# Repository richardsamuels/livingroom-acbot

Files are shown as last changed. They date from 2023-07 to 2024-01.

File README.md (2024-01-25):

# AC Bot
An ESPHome-based robot to integrate my GE AEL08LQQ2 window AC into Home Assistant.

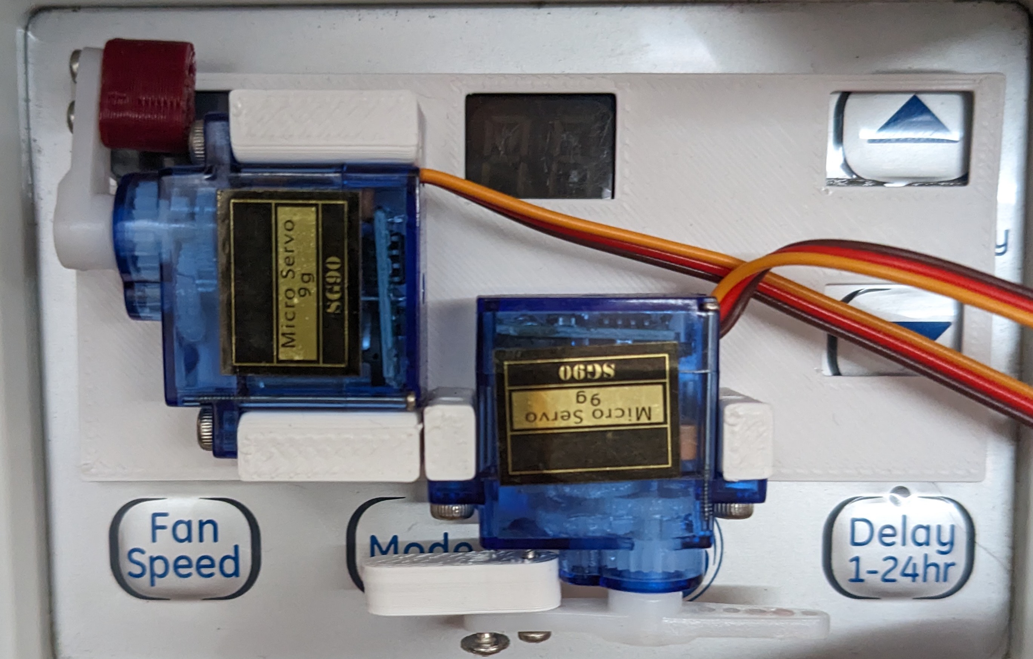
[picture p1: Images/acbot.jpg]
ACbot installed in place


## Custom PCB
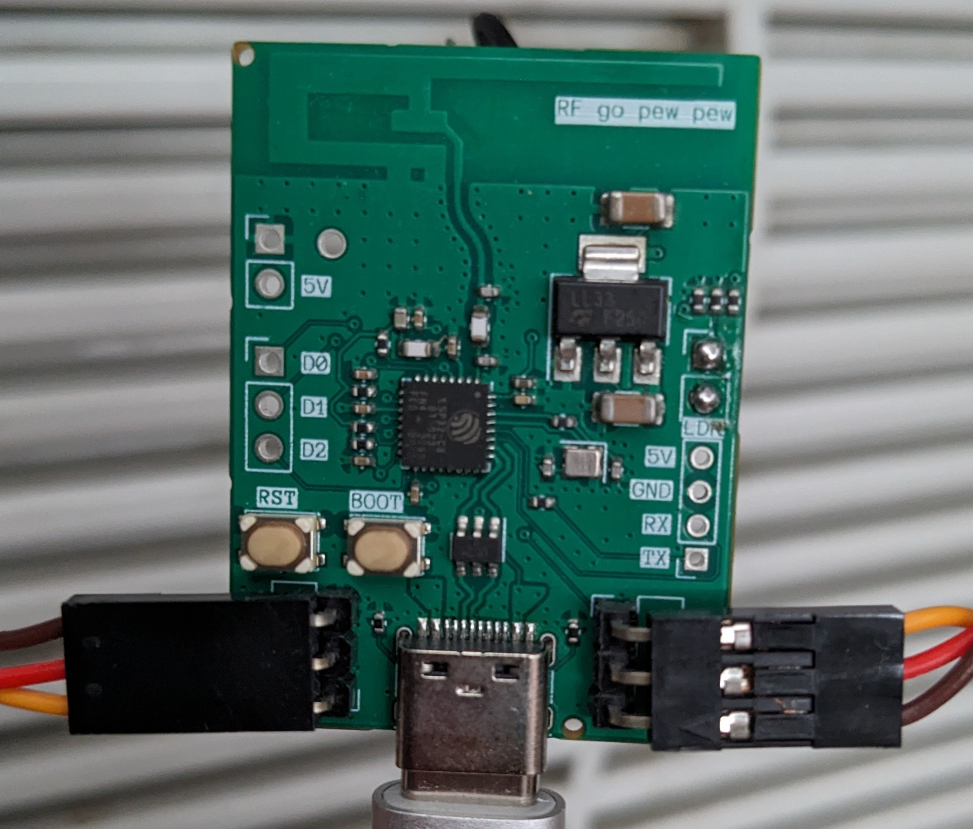
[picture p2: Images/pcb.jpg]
PCB


A custom PCB can be found in ./PCB. The expected servo pinout is (Control, 5V, GND),
where Control is indicated on the silkscreen with a solid colored pin.

## BOM

Note: This BOM does not include parts on custom PCB. See the JLCPCB-compatible
[PCB BOM](PCB/jlcpcb/production_files/BOM-esp.csv) for those items, which can
be used to purchase a fully assembled PCB from JLCPCB.

| Part | Quantity |
| --- | --- |
| SG90 Servo | 2 |
| M2.5x6 SHCS | 4 |
| M2x10 self-tapping screws | 5 |
| [~Photoresistor~*](https://www.amazon.com/gp/product/B01N7V536K) | 1 |
| STL/panel.stl, any stiff filament (ABS, PLA, or PETG) | 1 |
| STL/power-pusher.stl, any stiff filament (ABS, PLA, or PETG) | 2 |

* The original version of this PCB used a photoresistor to detect the on/off
state of the AC, see below for the flaws of this approach

## 3D Printed Parts

1. Connect all servos to the flashed PCB and apply power via USB-C to zero the
servo positions.
2. To each servo, attach power-pusher.stl to the servo horn with a single arm
using M2x10 self-tappers. Use the hole farthest from the center, and third from
the end.
3. Attach servos with M2.5x6 SHCS bolts to panel.stl. Screw directly into the
plastic.
4. Using VHB, or similarly strong double-sided sticky tape, attach directly to
AC's front panel, ensuring alignment with the power, temperature read out, and
temperature control buttons.
5. Press the panel down with even more force to ensure the servos will not push
the printed parts off the front panel.

## Failed Approaches
1. This project originally used a photoresistor to detect when the temperature
readout was lit to infer the on/off state of the air conditioner. This approach
proved unreliable because the outer plastic shell of the airconditioner is
translucent to sunlight, and would provide false indications when the sun
shined directly on the air conditioner's shell.

This was remediated with an [Aqara Smart Plug](https://www.amazon.com/gp/product/B07CJ2MM6Z)
which reports the power consumption in watts.. If the AC is consuming more than
50 watts, it is considered to be on; otherwise, it is considered to be off.

2 . The original version of this project offered the ability to change the
temperature instead of the AC mode (Cool/Energy Save/Fan). After putting v1
into action, I did not use the remote temperature change functionality, but
wanted to change the mode. This functionality was dropped, and the servo was
repurposed to allow changing the mode instead.

## Future Work
1. Change the AC Mode instead of turning off the entire unit when Home
Assistant's thermostat is used.
2. Design a proper mounting mechanism for the PCB, and a cover for the whole
unit

# Setup & Flashing
## Setup
1. `python -m venv venv`
2. `./venv/bin/activate`
3. `python -m pip install esphome`
## Flashing
`esphome run livingroom-acbot.yaml`

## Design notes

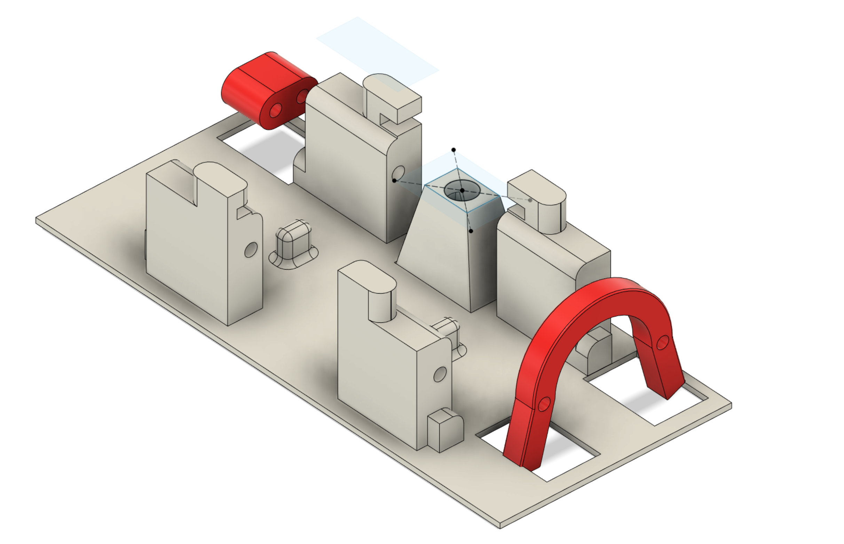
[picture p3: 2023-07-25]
Images/fusion.png

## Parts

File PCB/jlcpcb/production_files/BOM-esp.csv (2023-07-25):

Comment | Designator | Footprint | LCSC
22uF | C301,C302 | C_1206_3216Metric | C12891
10n | C204 | C_0402_1005Metric | C15195
0.1u | C206,C207,C208,C209,C210,C211 | C_0402_1005Metric | C1525
12p | C212,C213 | C_0402_1005Metric | C1547
10u | C205 | C_0402_1005Metric | C15525
3p3 | C201,C202 | C_0402_1005Metric | C1565
USB_C_Plug_USB2.0 | P301 | USB_C_Receptacle_HRO_TYPE-C-31-M-12 | C165948
22R | R207 | R_0402_1005Metric | C25092
470R | R201 | R_0402_1005Metric | C25117
Crystal_GND24 | Y201 | Crystal_SMD_2016-4Pin_2.0x1.6mm | C255898
5k1 | R202,R203,R204,R205,R206,R301,R302,R303,R304 | R_0402_1005Metric | C25905
2n2 | L201,L202 | L_0603_1608Metric | C29682
LDL111733R | U301 | SOT-223-3_TabPin2 | C435835
SW_Push | SW201,SW202 | SW_SPST_PTS810 | C470426
ESP32-C3FN4 | U201 | QFN-32-1EP_5x5mm_P0.5mm_EP3.45x3.45mm | C5143572
1u | C203 | C_0402_1005Metric | C52923
USBLC6-2SC6 | U302 | SOT-23-6 | C7519
Conn_01x03_Pin | J101,J102 | PinHeader_1x03_P2.54mm_Horizontal | C92159
50k | R101 | PinHeader_1x02_P2.54mm_Vertical
2.4GHz aerial | AE201 | Texas_SWRU120D_InvF_2.4GHz_Right
Conn_01x04_Socket | J104 | PinSocket_1x04_P2.00mm_Vertical
Conn_01x03_Socket | J105 | PinHeader_1x03_P2.54mm_Vertical
Conn_01x02_Socket | J103 | PinHeader_1x02_P2.54mm_Vertical

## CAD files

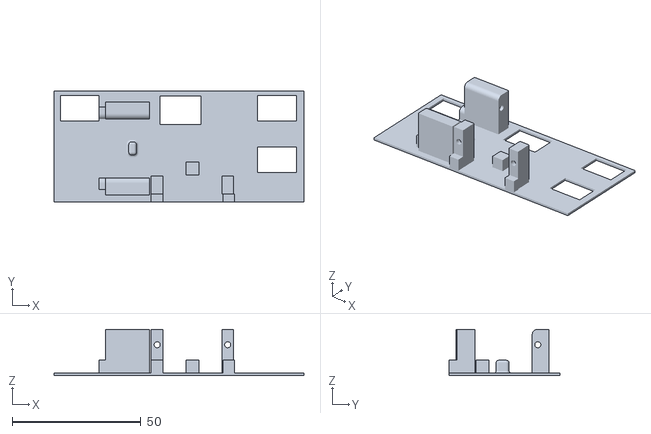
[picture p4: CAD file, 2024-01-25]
STL/panel.stl
97.0 x 43.0 x 18.0

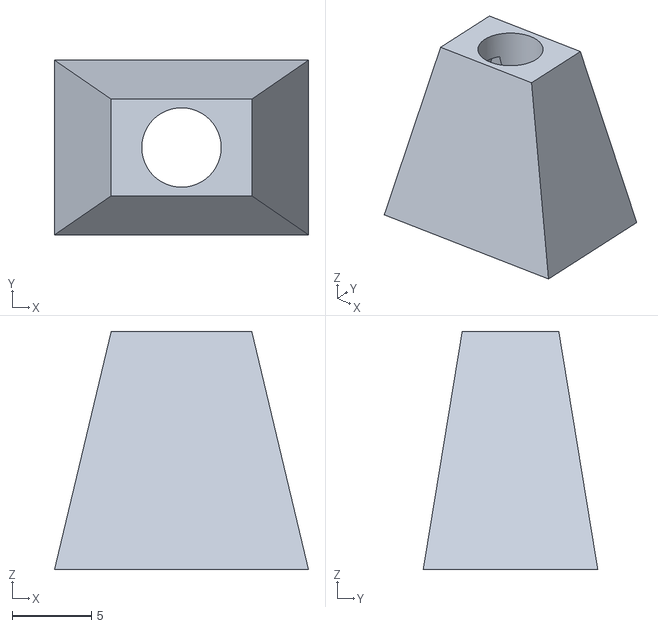
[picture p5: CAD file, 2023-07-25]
STL/photoresistor-guide.stl
16.0 x 11.0 x 15.0

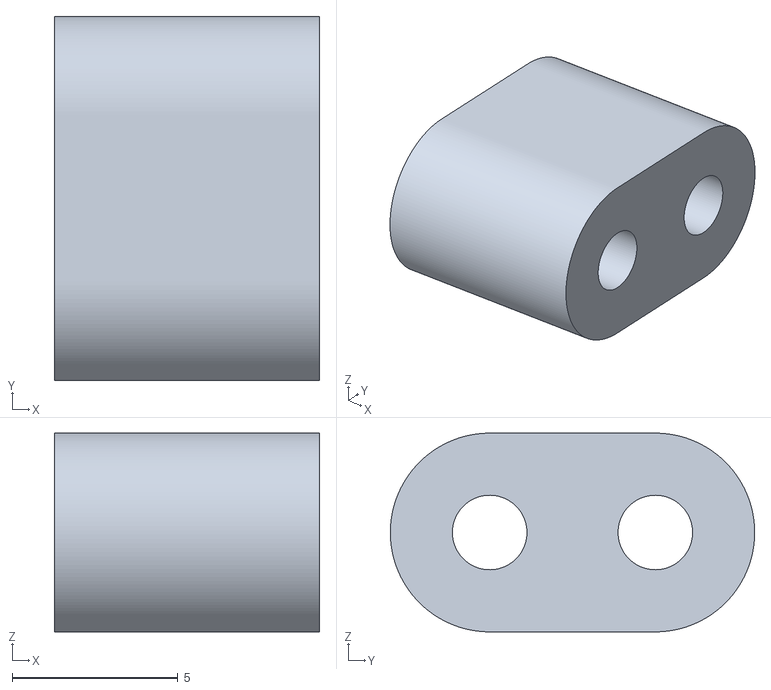
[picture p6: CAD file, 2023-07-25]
STL/power-pusher.stl
8.00 x 11.0 x 6.00

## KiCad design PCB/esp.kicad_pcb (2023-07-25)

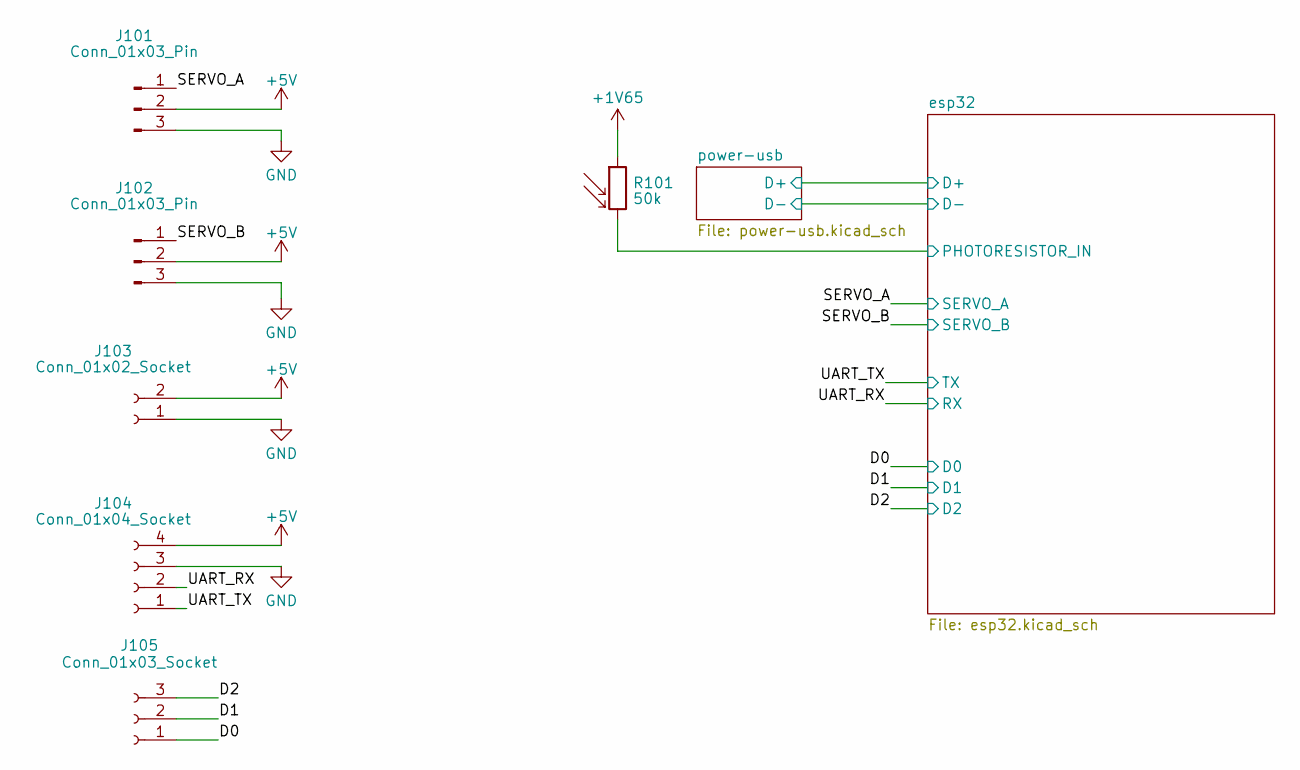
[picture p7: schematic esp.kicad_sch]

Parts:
J101, J102: Conn_01x03_Pin; PinHeader_1x03_P2.54mm_Horizontal
J103: Conn_01x02_Socket; PinHeader_1x02_P2.54mm_Vertical
J104: Conn_01x04_Socket; PinSocket_1x04_P2.00mm_Vertical
J105: Conn_01x03_Socket; PinHeader_1x03_P2.54mm_Vertical
R101: 50k; PinHeader_1x02_P2.54mm_Vertical

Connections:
+1V65: R101.1; also elsewhere on the board
+5V: J101.2, J102.2, J103.2, J104.4; also elsewhere on the board
/D0: J105.1; also elsewhere on the board
/D1: J105.2; also elsewhere on the board
/D2: J105.3; also elsewhere on the board
/SERVO_A: J101.1; also elsewhere on the board
/SERVO_B: J102.1; also elsewhere on the board
/UART_RX: J104.2; also elsewhere on the board
/UART_TX: J104.1; also elsewhere on the board
/esp32/PHOTORESISTOR_IN: R101.2; also elsewhere on the board
GND: J101.3, J102.3, J103.1, J104.3; also elsewhere on the board

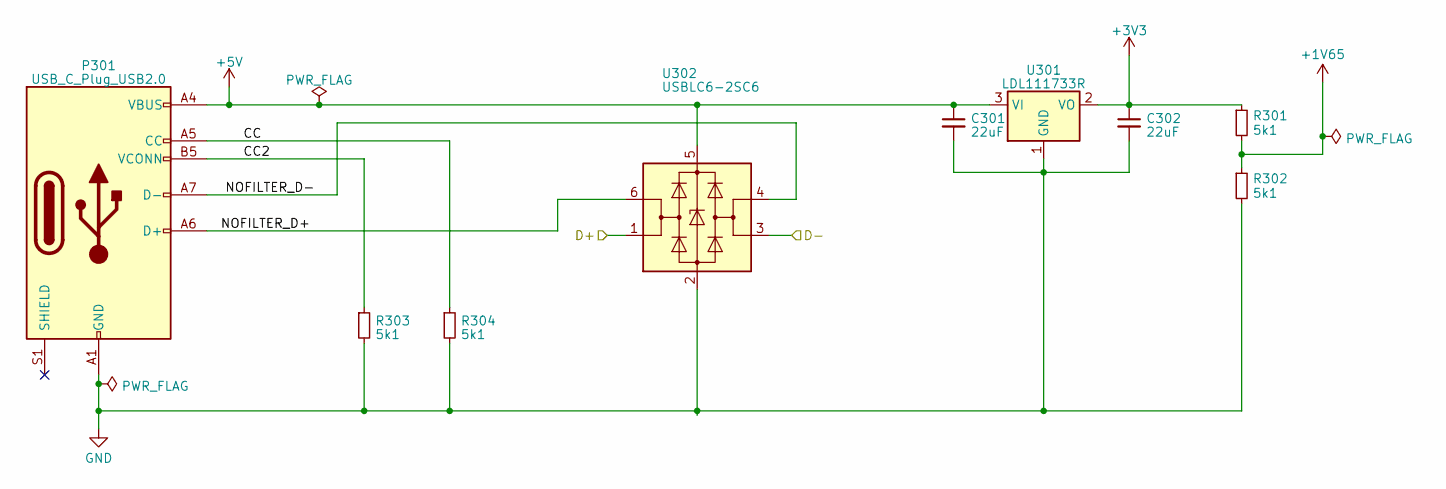
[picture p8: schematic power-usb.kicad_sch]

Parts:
C301, C302: 22uF; C_1206_3216Metric
P301: USB_C_Plug_USB2.0; USB_C_Receptacle_HRO_TYPE-C-31-M-12
R301, R302, R303, R304: 5k1; R_0402_1005Metric
U301: LDL111733R; SOT-223-3_TabPin2
U302: USBLC6-2SC6; SOT-23-6

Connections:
+1V65: R301.2, R302.1; also elsewhere on the board
+3V3: C302.1, R301.1, U301.2 (VO); also elsewhere on the board
+5V: C301.1, P301.A4 (VBUS), P301.A9 (VBUS), P301.B4 (VBUS), P301.B9 (VBUS), U301.3 (VI), U302.5 (VBUS); also elsewhere on the board
/esp32/D+: U302.1 (I/O1); also elsewhere on the board
/esp32/D-: U302.3 (I/O2); also elsewhere on the board
/power-usb/CC: P301.A5 (CC), R304.1
/power-usb/CC2: P301.B5 (VCONN), R303.1
/power-usb/NOFILTER_D+: P301.A6 (D+), P301.B6 (D+), U302.6 (I/O1)
/power-usb/NOFILTER_D-: P301.A7 (D-), P301.B7 (D-), U302.4 (I/O2)
GND: C301.2, C302.2, P301.A1 (GND), P301.A12 (GND), P301.B1 (GND), P301.B12 (GND), R302.2, R303.2, R304.2, U301.1 (GND), U302.2 (GND); also elsewhere on the board

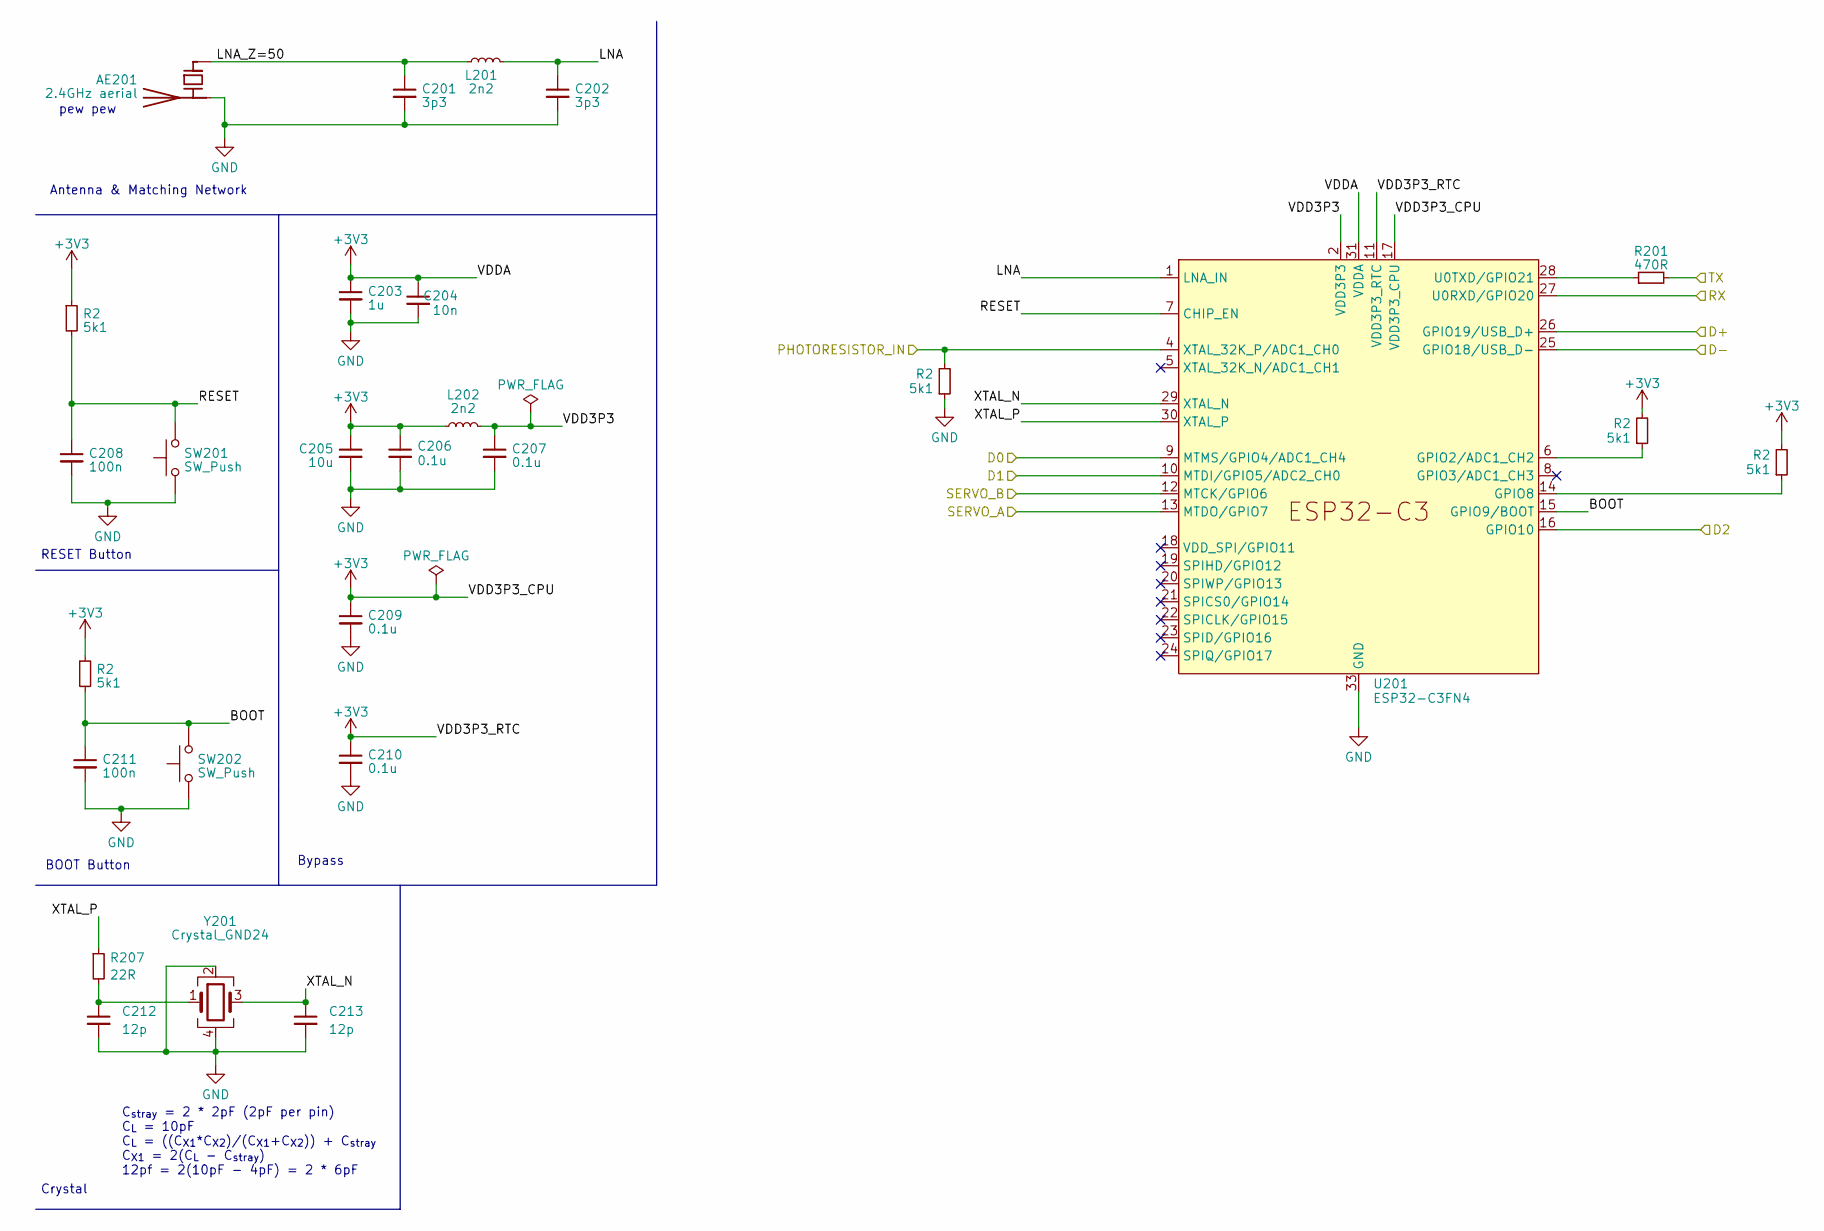
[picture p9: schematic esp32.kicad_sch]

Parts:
AE201: 2.4GHz aerial; Texas_SWRU120D_InvF_2.4GHz_Right
C201, C202: 3p3; C_0402_1005Metric
C203: 1u; C_0402_1005Metric
C204: 10n; C_0402_1005Metric
C205: 10u; C_0402_1005Metric
C206, C207, C209, C210: 0.1u; C_0402_1005Metric
C208, C211: 100n; C_0402_1005Metric
C212, C213: 12p; C_0402_1005Metric
L201, L202: 2n2; L_0603_1608Metric
R2: 5k1; R_0402_1005Metric
R201: 470R; R_0402_1005Metric
R207: 22R; R_0402_1005Metric
SW201, SW202: SW_Push; SW_SPST_PTS810
U201: ESP32-C3FN4; QFN-32-1EP_5x5mm_P0.5mm_EP3.45x3.45mm
Y201: Crystal_GND24; Crystal_SMD_2016-4Pin_2.0x1.6mm

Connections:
+3V3: C203.1, C204.1, C205.1, C206.1, C209.1, C210.1, L202.1, U201.11 (VDD3P3_RTC), U201.17 (VDD3P3_CPU), U201.31 (VDDA), U201.32 (VDDA); also elsewhere on the board
/D0: U201.9 (MTMS/GPIO4/ADC1_CH4); also elsewhere on the board
/D1: U201.10 (MTDI/GPIO5/ADC2_CH0); also elsewhere on the board
/D2: U201.16 (GPIO10); also elsewhere on the board
/SERVO_A: U201.13 (MTDO/GPIO7); also elsewhere on the board
/SERVO_B: U201.12 (MTCK/GPIO6); also elsewhere on the board
/UART_RX: U201.27 (U0RXD/GPIO20); also elsewhere on the board
/UART_TX: R201.2; also elsewhere on the board
/esp32/BOOT: C211.1, SW202.2, U201.15 (GPIO9/BOOT); also elsewhere on the board
/esp32/D+: U201.26 (GPIO19/USB_D+); also elsewhere on the board
/esp32/D-: U201.25 (GPIO18/USB_D-); also elsewhere on the board
/esp32/LNA: C202.1, L201.2, U201.1 (LNA_IN)
/esp32/LNA_Z=50: AE201.1 (FEED), C201.1, L201.1
/esp32/PHOTORESISTOR_IN: U201.4 (XTAL_32K_P/ADC1_CH0); also elsewhere on the board
/esp32/RESET: C208.1, SW201.2, U201.7 (CHIP_EN); also elsewhere on the board
/esp32/VDD3P3: C207.1, L202.2, U201.2 (VDD3P3), U201.3 (VDD3P3)
/esp32/XTAL_N: C213.1, U201.29 (XTAL_N), Y201.3
/esp32/XTAL_P: R207.1, U201.30 (XTAL_P)
GND: AE201.2 (PCB_Trace), C201.2, C202.2, C203.2, C204.2, C205.2, C206.2, C207.2, C208.2, C209.2, C210.2, C211.2, C212.2, C213.2, SW201.1, SW202.1, U201.33 (GND), Y201.2, Y201.4; also elsewhere on the board
unnamed: C212.1, R207.2, Y201.1
unnamed 26: U201.6 (GPIO2/ADC1_CH2); also elsewhere on the board
unnamed 27: U201.14 (GPIO8); also elsewhere on the board
unnamed: R201.1, U201.28 (U0TXD/GPIO21)

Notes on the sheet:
Antenna & Matching Network
C_{stray} = 2 * 2pF (2pF per pin) C_{L} = 10pF C_{L} = ((C_{X1}*C_{X2})/(C_{X1}+C_{X2})) + C_{stray} C_{X1} = 2(C_{L} - C_{stray}) 12pf = 2(10pF - 4pF) = 2 * 6pF
Crystal
RESET Button
Bypass
BOOT Button
pew pew

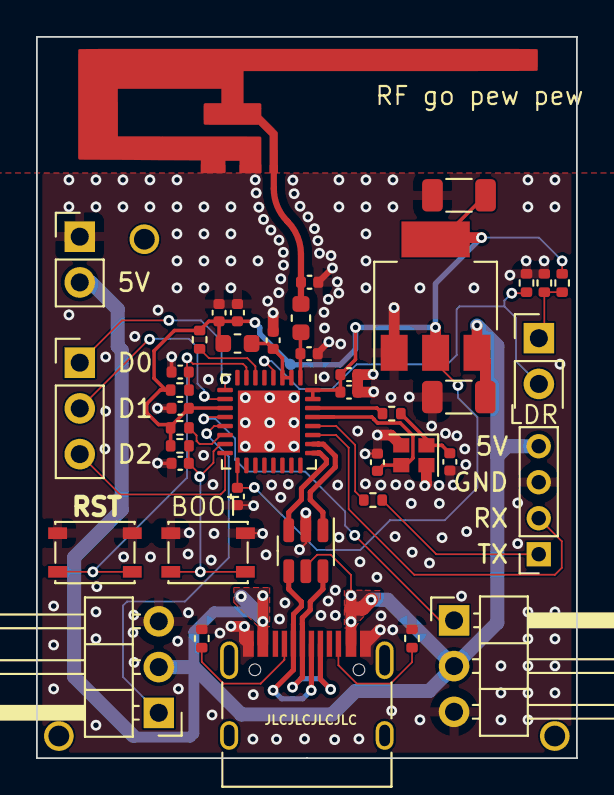
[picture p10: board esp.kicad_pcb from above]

Board: 4 copper layers, 30.0 x 40.1 mm, 42 parts (0 on the bottom side), 29 nets.

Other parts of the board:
R202, R203, R204, R205, R206: 5k1; R_0402_1005Metric

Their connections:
+3V3: R202.1, R204.2, R205.2, R206.1; also elsewhere on the board
/esp32/BOOT: R206.2; also elsewhere on the board
/esp32/PHOTORESISTOR_IN: R203.2; also elsewhere on the board
/esp32/RESET: R202.2; also elsewhere on the board
GND: R203.1; also elsewhere on the board
unnamed 26: R204.1; also elsewhere on the board
unnamed 27: R205.1; also elsewhere on the board

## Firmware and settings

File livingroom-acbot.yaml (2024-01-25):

esphome:
  name: livingroom-acbot3
  includes:
    - helpers.hpp
  platformio_options:
    board_build.flash_mode: dio
    board_build.f_flash: 40000000L
    board_build.flash_size: 4MB
  on_boot:
    # reset servo positions on boot
    - priority: 600
      then:
        - servo.write:
            id: mode_select
            level: 0
        - servo.write:
            id: power
            level: 0
    # work around for esphome issue #3688
    # https://github.com/esphome/issues/issues/3668#issuecomment-1493423796
    - priority: 500
      then:
        - esp32_ble_tracker.stop_scan:
    - priority: 100
      then:
        - delay: 10s
        - esp32_ble_tracker.start_scan:
            continuous: true

preferences:
  flash_write_interval: 70s

esp32:
  board: esp32-c3-devkitm-1
  variant: esp32c3
  framework:
    type: esp-idf

logger:
  #level: VERY_VERBOSE
  logs:
    esp-idf: ERROR

<<: !include "secrets.yaml"

servo:
  - id: power
    output: power_servo_output
  - id: mode_select
    output: mode_select_servo_output

output:
  - platform: ledc
    id: power_servo_output
    pin: GPIO6
    frequency: 50Hz
  - platform: ledc
    id: mode_select_servo_output
    pin: GPIO7
    frequency: 50Hz

sensor:
  - platform: homeassistant
    id: ac_power
    entity_id: sensor.living_room_ac_power

number:
  - platform: template
    internal: true
    name: AC Power Servo
    min_value: -100
    initial_value: 0
    max_value: 100
    step: 1
    optimistic: true
    set_action:
      then:
        - servo.write:
            id: power
            level: !lambda 'return x / 100.0;'

button:
  - platform: template
    name: Living Room AC
    # toggle the AC power button
    id: living_room_ac_power_toggle
    internal: true
    on_press:
      - servo.write:
          id: power
          level: 0.45
      - delay: 250ms
      - servo.write:
          id: power
          level: 0.0
      - delay: 250ms
  # XXX: If living_room_ac_mode is called multiple times, the servo actions will
  # not batch, but will instead clobber one another. These seemingly duplicate
  # functions are a workaround for this issue when it is necessary to call
  # living_room_ac_mode multiple times in row.
  - platform: template
    # toggle the AC mode button
    name: Living Room AC Mode
    id: living_room_ac_mode
    internal: true
    on_press:
      - servo.write:
          id: mode_select
          level: 0.40
      - delay: 250ms
      - servo.write:
          id: mode_select
          level: 0.0
      - delay: 250ms
  - platform: template
    name: Living Room AC Mode 2
    id: living_room_ac_mode_2
    internal: true
    on_press:
      - servo.write:
          id: mode_select
          level: 0.40
      - delay: 250ms
      - servo.write:
          id: mode_select
          level: 0.0
      - delay: 250ms
      - servo.write:
          id: mode_select
          level: 0.40
      - delay: 250ms
      - servo.write:
          id: mode_select
          level: 0.0
      - delay: 250ms
  - platform: template
    name: Living Room AC Mode 3
    id: living_room_ac_mode_3
    internal: true
    on_press:
      - servo.write:
          id: mode_select
          level: 0.40
      - delay: 250ms
      - servo.write:
          id: mode_select
          level: 0.0
      - delay: 250ms
      - servo.write:
          id: mode_select
          level: 0.40
      - delay: 250ms
      - servo.write:
          id: mode_select
          level: 0.0
      - delay: 250ms
      - servo.write:
          id: mode_select
          level: 0.40
      - delay: 250ms
      - servo.write:
          id: mode_select
          level: 0.0
      - delay: 250ms

switch:
  - platform: template
    id: living_room_ac
    icon: 'mdi:air-conditioner'
    name: "AC"
    lambda: !lambda "return id(ac_power).state >= 50;"
    restore_mode: RESTORE_DEFAULT_OFF
    turn_on_action:
      - button.press: living_room_ac_power_toggle
    turn_off_action:
      - button.press: living_room_ac_power_toggle
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

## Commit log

2023-05-29 Prototype w/ FREENOVE ESP32-WROVER cam board
2023-06-07 use a pull down for the adc
2023-07-25 Add Custom PCB (#2)
    [BOM-esp.csv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]
2024-01-25 V2, with support for mode changing (#3)
    [panel.stl, updown-pusher.stl]
